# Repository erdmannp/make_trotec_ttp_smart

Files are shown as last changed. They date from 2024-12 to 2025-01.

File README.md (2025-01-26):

# Trotec TTP5 Dehumidifier

I bought a used Troted TTP5, which is a peltier based dehumidifier. It is absolutely sufficient for small rooms like my bathroom. But it only has two modes: On and Off. The original PCB looks like this:

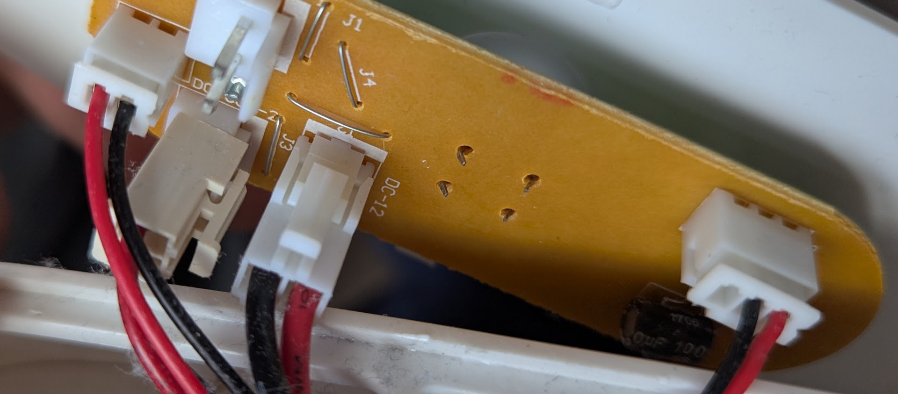
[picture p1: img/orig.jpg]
Original


The 9 Volt input power is connected to the "DC-12" port. Peltier and Fan are connected in the left of this image. The connector on the right is the "water level high" switch. In this model it is literally a switch which is turned on by a high water level. 

My idea is to take the "water level high" signal input and "reuse" it as the enable or disable of the dehumidifier. So when turned on the dehumidifier will no longer be on, it will only be used if the humidity sensor shows a value below the threshold. 
The TTP5 PCB will act like the watertank is full, in case of low humidity or watertank full.

I designed the PCB in a way that it is piggybacked by the normal PCB:

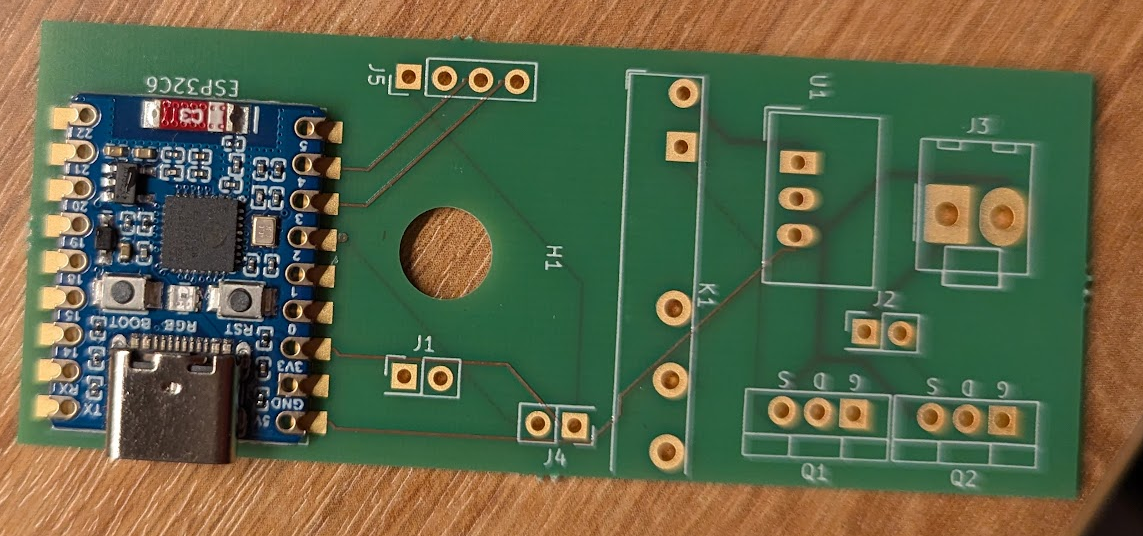
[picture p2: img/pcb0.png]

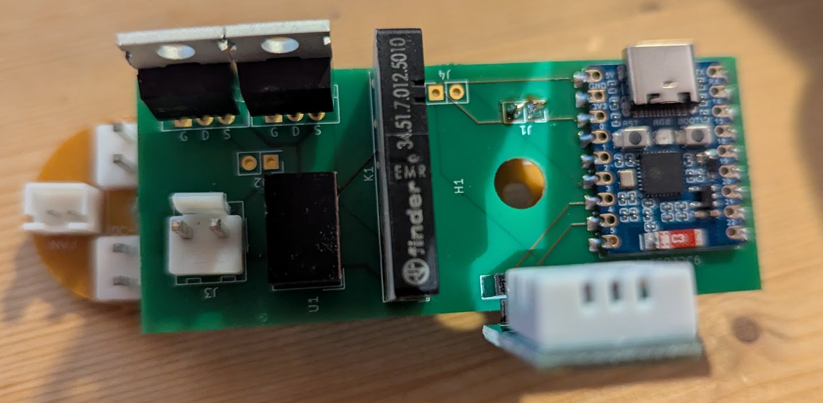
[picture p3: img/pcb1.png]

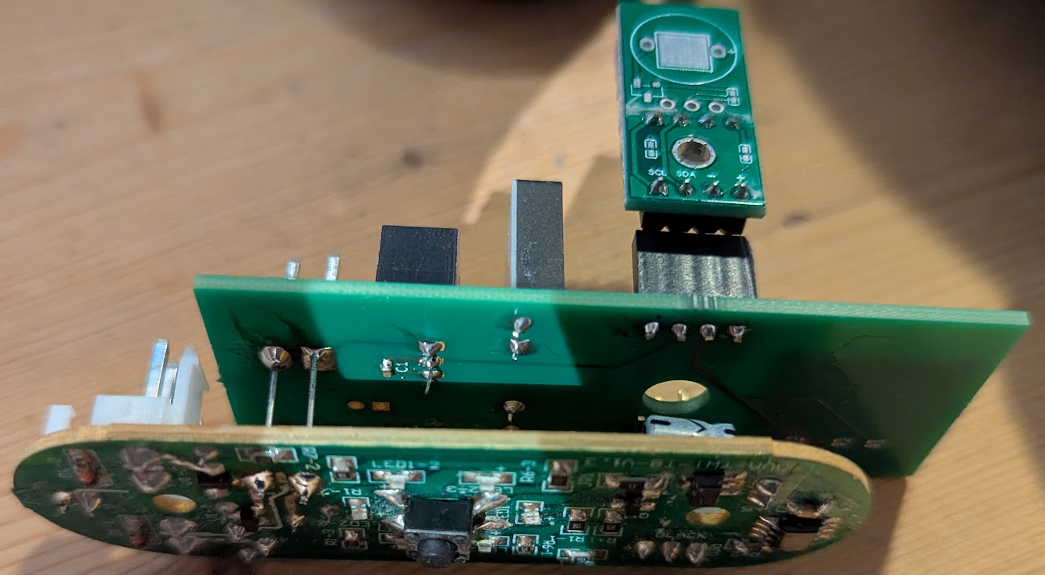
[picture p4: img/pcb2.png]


The "water level high" signal is now handled by the added PCB.

After a testphase I connected the humidity sensor inside of the TTP5 chassis. 

The configuration Webinterface is very rudimental, but it does the job.

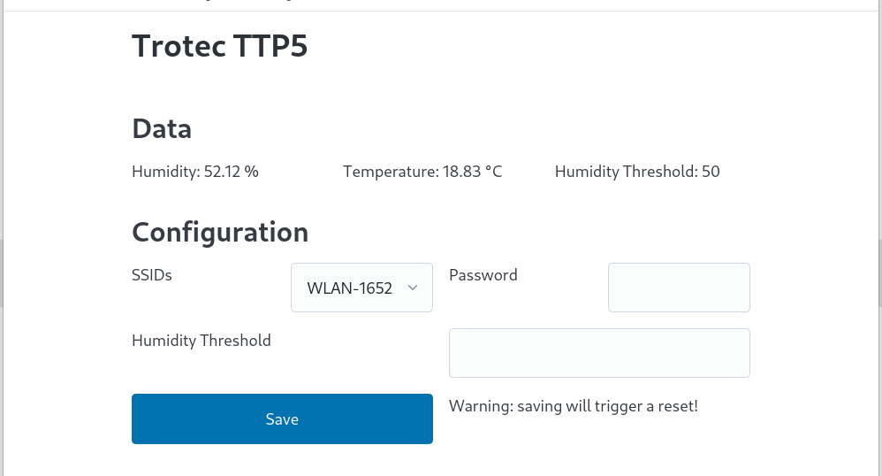
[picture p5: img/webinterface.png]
Webinterface


# To Do's

- Display the waterlevel status on webpage.
- Display the current status (peltier and fan On or Off).
- Add MQTT protocol and support.
- Add a small pump and connect it to the sewer pipe.

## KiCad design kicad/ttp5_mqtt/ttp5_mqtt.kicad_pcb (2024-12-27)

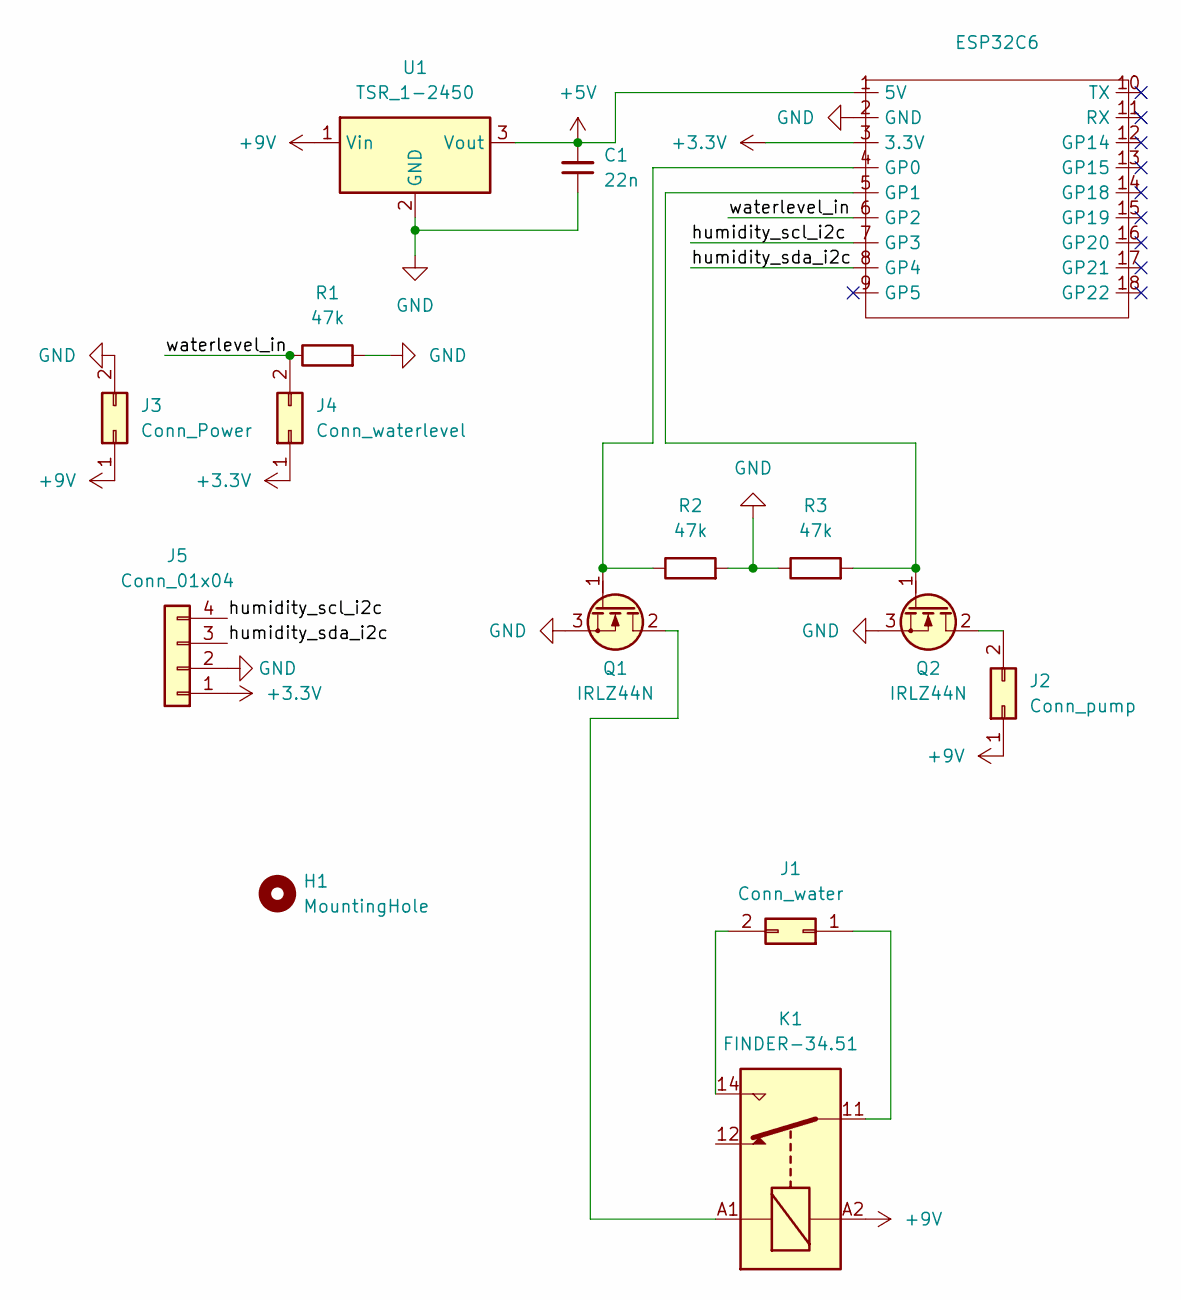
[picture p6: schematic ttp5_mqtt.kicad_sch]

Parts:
C1: 22n; R_0603_1608Metric_Pad0.98x0.95mm_HandSolder
ESP32C6: Waveshare ESP32-C6 Mini Development Board
H1: MountingHole; MountingHole_6.5mm
J1: Conn_water; PinHeader_2x01_P2.54mm_Vertical
J2: Conn_pump; PinHeader_2x01_P2.54mm_Vertical
J3: Conn_Power; Molex_KK-396_A-41791-0002_1x02_P3.96mm_Vertical
J4: Conn_waterlevel; PinHeader_2x01_P2.54mm_Vertical
J5: Conn_01x04; PinHeader_1x04_P2.54mm_Vertical
K1: FINDER-34.51; Relay_SPDT_Finder_34.51_Vertical
Q1, Q2: IRLZ44N; TO-220-3_Vertical_GDS
R1, R2, R3: 47k; R_0201_0603Metric_Pad0.64x0.40mm_HandSolder
U1: TSR_1-2450; Converter_DCDC_TRACO_TSR-1_THT

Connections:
+3.3V: ESP32C6.3 (3.3V), J4.1, J5.1
+5V: C1.2, ESP32C6.1 (5V), U1.3 (Vout)
+9V: J2.1, J3.1, K1.A2, U1.1 (Vin)
/humidity_scl_i2c: ESP32C6.7 (GP3), J5.4
/humidity_sda_i2c: ESP32C6.8 (GP4), J5.3
/waterlevel_in: ESP32C6.6 (GP2), J4.2, R1.1
GND: C1.1, ESP32C6.2 (GND), J3.2, J5.2, Q1.3 (S), Q2.3 (S), R1.2, R2.2, R3.1, U1.2 (GND)
unnamed: ESP32C6.4 (GP0), Q1.1 (G), R2.1
unnamed: ESP32C6.5 (GP1), Q2.1 (G), R3.2
unnamed: J1.1, K1.11
unnamed: J1.2, K1.14
unnamed: J2.2, Q2.2 (D)
unnamed: K1.A1, Q1.2 (D)

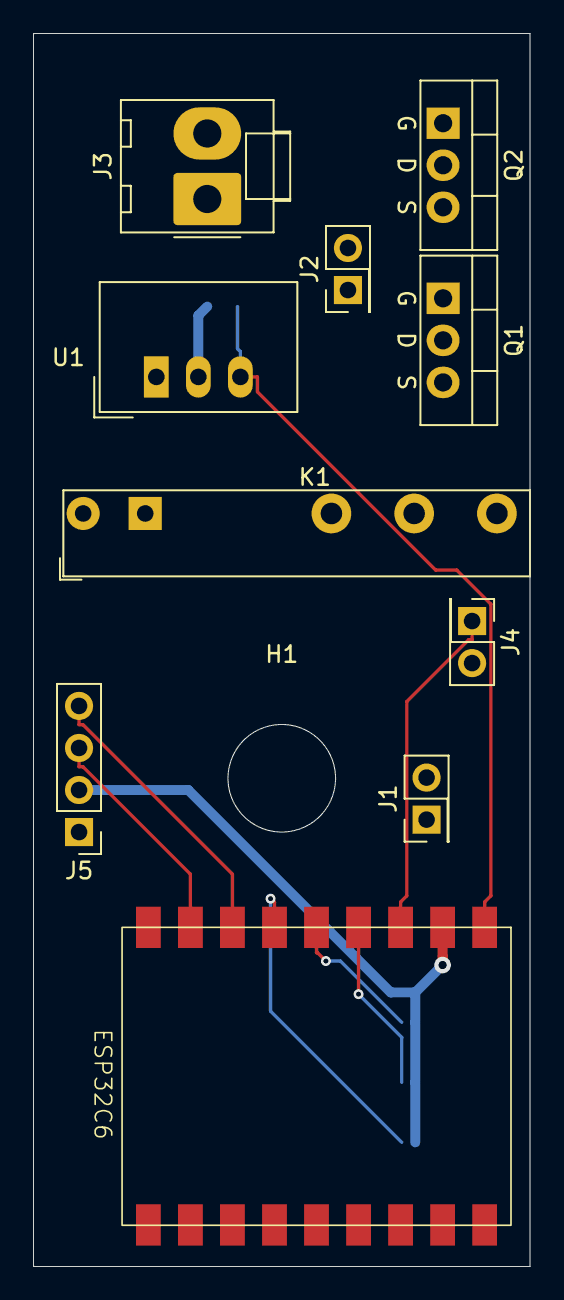
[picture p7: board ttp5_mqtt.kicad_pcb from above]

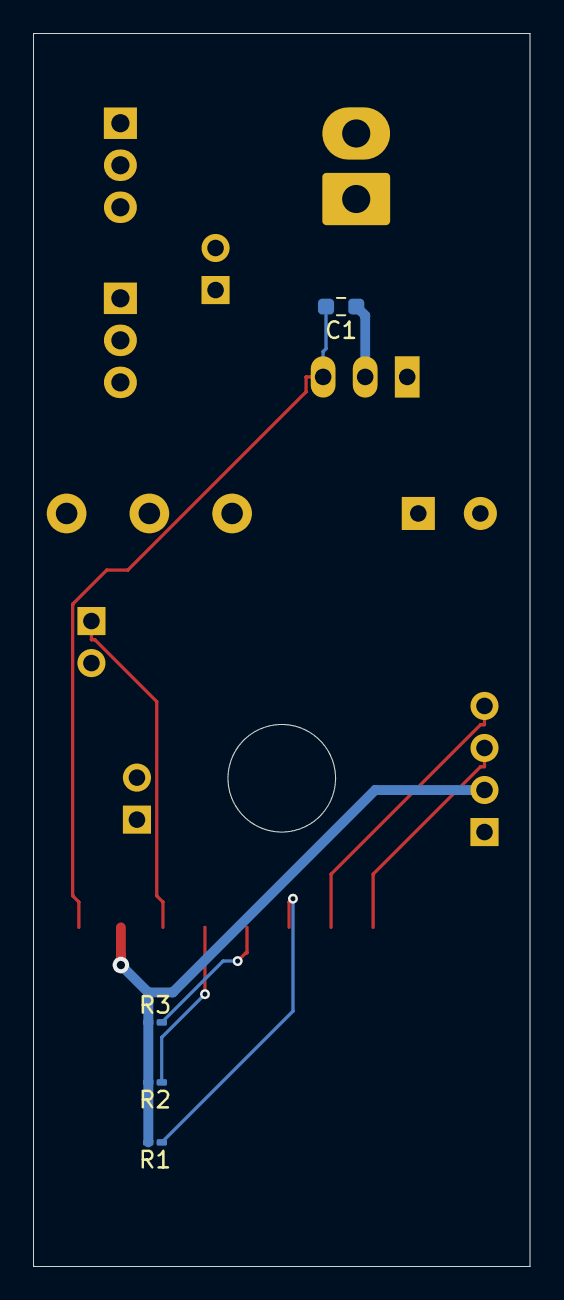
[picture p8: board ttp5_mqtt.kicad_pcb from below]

Board: 4 copper layers, 30.0 x 74.5 mm, 15 parts (4 on the bottom side), 13 nets.

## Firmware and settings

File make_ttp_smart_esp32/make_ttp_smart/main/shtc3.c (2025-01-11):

#include <stdio.h>
#include "sdkconfig.h"
#include "freertos/FreeRTOS.h"
#include "freertos/task.h"
#include "esp_log.h"
#include "driver/i2c.h"

#include "shtc3.h"


const static char *TAG = "shtc3";
const static uint16_t SHTC3_ADDR = 0x70;
const static uint32_t SHTC3_FREQ = 10000;
const static gpio_num_t I2C_MASTER_SDA_IO = 4;
const static gpio_num_t I2C_MASTER_SCL_IO = 3;



static const shtc3_t shtc3_empty_data = {
    .temperature = 0,
    .humidity = 0,
    .error = ESP_ERR_NOT_FINISHED,
};
static shtc3_t shtc3_data;


esp_err_t shtc3_init(void) {
    esp_err_t ret;

    i2c_config_t config = {
        .mode = I2C_MODE_MASTER,
        .sda_io_num = I2C_MASTER_SDA_IO,
        .scl_io_num = I2C_MASTER_SCL_IO,
        .sda_pullup_en = GPIO_PULLUP_ENABLE,
        .scl_pullup_en = GPIO_PULLUP_ENABLE,
        .master.clk_speed = SHTC3_FREQ,
    };
    ret = i2c_param_config(I2C_NUM_0, &config);
    ret += i2c_driver_install(I2C_NUM_0, config.mode, 0, 0, 0);


    return ret;
}


static void shtc3_wakeup(void) {
    uint8_t wakeup_command[] = {0x35, 0x17};
    i2c_cmd_handle_t cmd = i2c_cmd_link_create();
    i2c_master_start(cmd);
    i2c_master_write_byte(cmd, (SHTC3_ADDR << 1) | I2C_MASTER_WRITE, true);
    i2c_master_write(cmd, wakeup_command, sizeof(wakeup_command), true);
    i2c_master_stop(cmd);
    i2c_master_cmd_begin(I2C_NUM_0, cmd, 1000 / portTICK_PERIOD_MS);
    i2c_cmd_link_delete(cmd);
}

shtc3_t shtc3_static_read(void) {
    return shtc3_data;
}

static void shtc3_i2c_read(void) {
    uint8_t command[2] = {0x7C, 0xA2}; // normal mode
    uint8_t data[6];
    shtc3_data = shtc3_empty_data;
    
    shtc3_wakeup();


    i2c_cmd_handle_t cmd = i2c_cmd_link_create();
    i2c_master_start(cmd);
    i2c_master_write_byte(cmd, (SHTC3_ADDR << 1) | I2C_MASTER_WRITE, true);
    i2c_master_write(cmd, command, sizeof(command), true);
    i2c_master_start(cmd);
    i2c_master_write_byte(cmd, (SHTC3_ADDR << 1) | I2C_MASTER_READ, true);
    i2c_master_read(cmd, data, sizeof(data), I2C_MASTER_LAST_NACK);
    i2c_master_stop(cmd);
    esp_err_t ret = i2c_master_cmd_begin(I2C_NUM_0, cmd, 1000 / portTICK_PERIOD_MS);
    i2c_cmd_link_delete(cmd);

    if (ret == ESP_OK) {
        uint16_t temp_raw = (data[0] << 8) | data[1];
        uint16_t hum_raw = (data[3] << 8) | data[4];

        shtc3_data.temperature = -45 + 175 * ((float)temp_raw / 65535.0);
        shtc3_data.humidity = 100 * ((float)hum_raw / 65535.0);
        shtc3_data.error = ESP_OK;
    } else {
        shtc3_data.temperature = -300;
        shtc3_data.humidity = -300;
        shtc3_data.error = ret;
    }
}

void shtc3_task_f(void *arg) {
    const char *taskTag = "SHTC3Task";
    ESP_LOGI(taskTag, "SHTC3Task started");
    esp_err_t ret = shtc3_init();

    if (ret != ESP_OK) {
        ESP_LOGE(taskTag, "Error initializing SHTC3: %s", esp_err_to_name(ret));
        vTaskDelete(NULL);
       }

    while (1) {
        shtc3_i2c_read();
        if (shtc3_data.error != ESP_OK) {
            ESP_LOGE(taskTag, "Error reading SHTC3: %s", esp_err_to_name(shtc3_data.error));
        }
        vTaskDelay(200);
    }
}

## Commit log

2024-12-24 Add kicad files
    [ttp5_mqtt.kicad_pcb, ttp5_mqtt.kicad_sch]
2024-12-27 add sources
    [ttp5_mqtt.kicad_pcb, ttp5_mqtt.kicad_sch]
2025-01-11 Add configuration files and SHTC3 i2c reader
